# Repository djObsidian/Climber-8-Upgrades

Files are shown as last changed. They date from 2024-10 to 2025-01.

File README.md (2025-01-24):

# Climber-8-Upgrades
Some upgrades for the IDEX Climber-8A 3d printer. Includes improved printheads, direct drive extruder, print bed stabilization for high speed printing, configuration for Klipper with filament sensor support, fully functional COPY and MIRROR modes. 

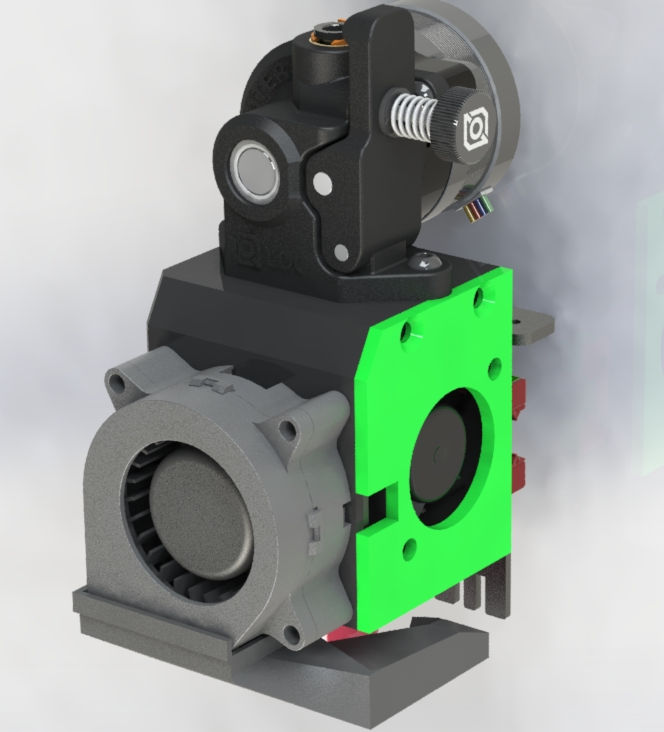
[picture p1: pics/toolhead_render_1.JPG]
Toolhead render


# Why?
Do you want to have two printers in one? Print with two completely different filaments? You don't like bedsilngers and prefer a faster and more compact printer? And not overpaying for a SnapMaker J1S or Ratrig V-Core? Then this upgrade kit is for you! Climber-8A is a very interesting 3D printer from aliexpress, the cheapest IDEX I could find that isn't a bedsilnger. Mechanically and electronically it is quite good, especially for its price, but has a number of flaws very undesirable in 2024, such as for example the bowden feed mechanism, low print speed, no input shaping and so on. This project is designed to fix them! 

# Printing 3d parts
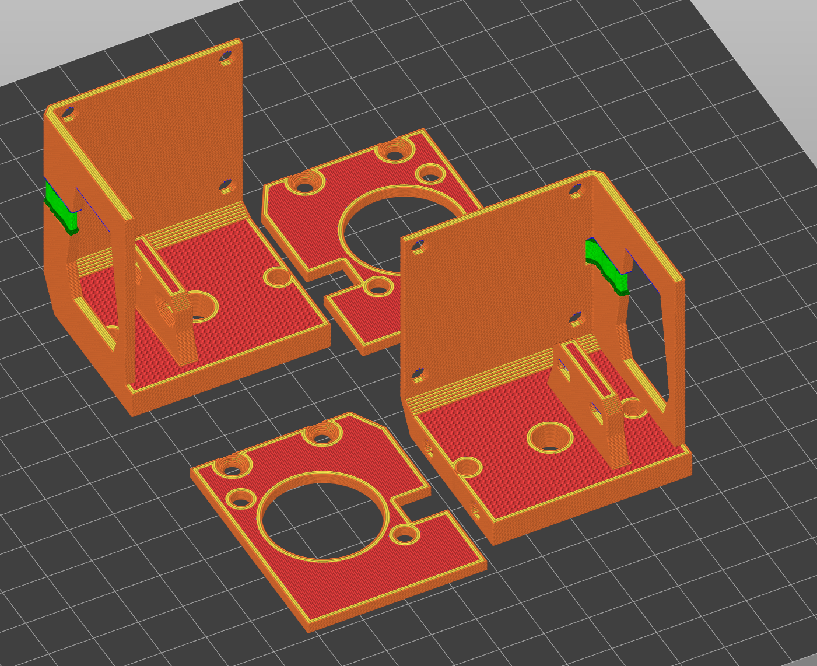
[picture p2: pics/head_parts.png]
Head parts

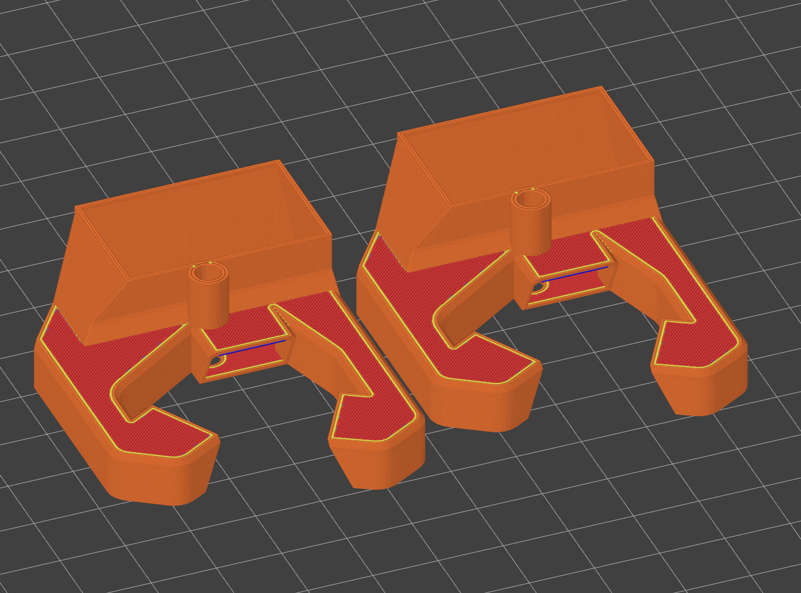
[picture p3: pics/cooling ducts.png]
Cooling ducts

You can find example print projects in *./toolhead* folder. They are configured for Creality K1. You may print everything as you want, but here're recommended settings:
| Parameter  | Value |
| --- | --- |
| Material  | ABS, ASA, PC, PA, or any other high temp non-flexible material  |
| Infill  | 80-100%  |
| Wall count | 3+ |
|Top/bottom layers| 3 for ducts, 4+ for toolhead|
| Layer height | <=0.12 for ducts, 0.2-0.28 for toolhead |
| Line width | 0.4-0.5 |
| Extra perimeters on overhangs | disabled for ducts |
| Thick bridges | enabled |

# Assembly instructions
[Illustrated step-by-step assembly instructions](assembly.md)

# Klipper config
Use following settings in order to compile MCU firmware. Flash as usual: rename file to firmware.bin, put it onto SD card, insert into 3d printer and boot. If you want to preserve original firmware, copy firmware.cur before flashing.
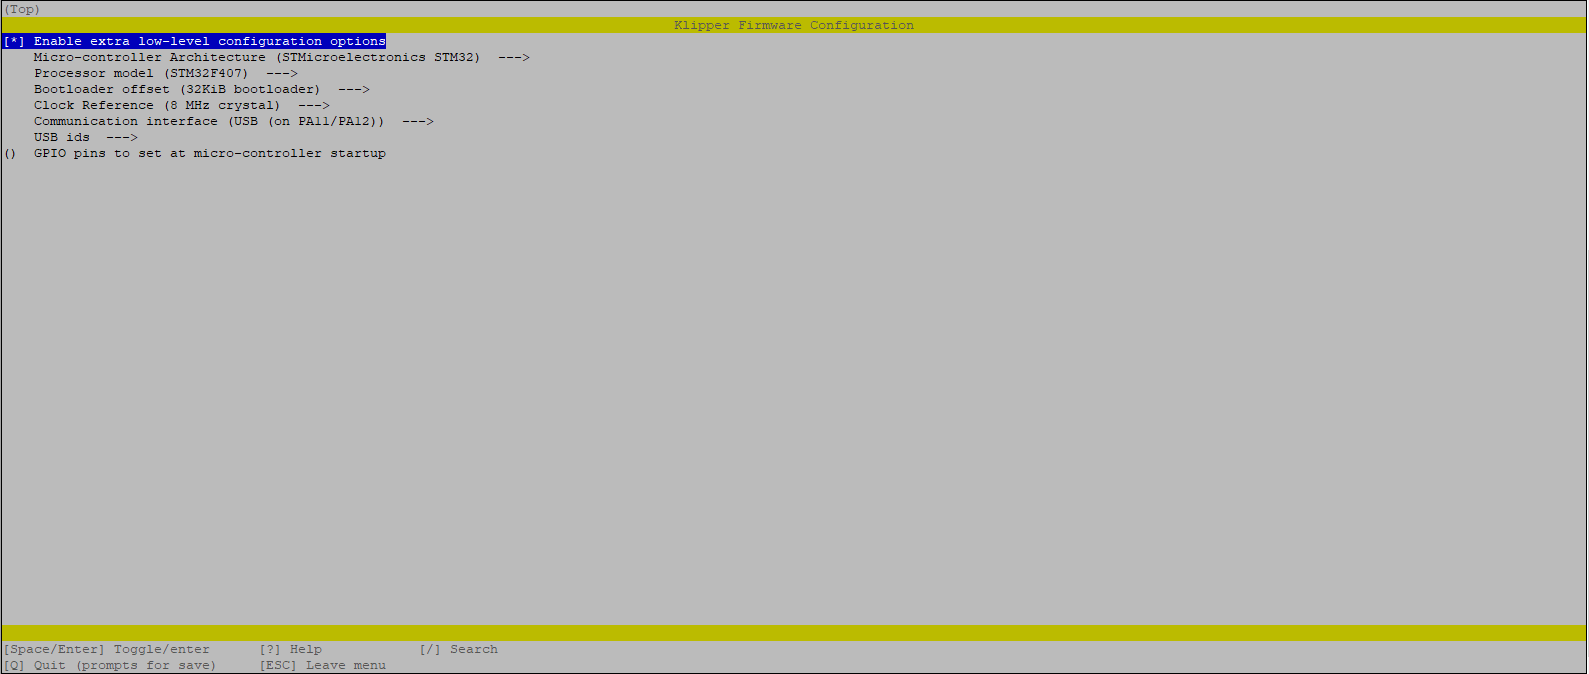
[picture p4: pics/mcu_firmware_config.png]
MCU config

Then simply import everything from klipper config folder. Change your [mcu] config accordingly. If you aren't using orbiter filament sensor, remove [include BOS.cfg] from printer.cfg. In this case you may want to write your own pause/resume macros. 

# Slicer config
Currentrly I support only prusaslicer. But porting to anything based on it shouldn't be too complicated.
Just import [normal mode](./prusaslicer%20config/config_normal_mode.ini) and [copy mode](./prusaslicer%20config/config_copy_mode.ini) into prusaslicer and set custom bed 3d model to [climber8 platform](./prusaslicer%20config/climber8_platform.STL).

# TODO Repo list
- [ ] Add BOM
- [X] Add assembly instructions
- [x] Add configuration instructions
- [x] Add parts printing instructions
- [x] Add slicer profiles
- [ ] Add board pinout and photos
- [ ] Add links to other people's used works

# TODO Project list
- [ ] Add spool holders and feed tubes
- [ ] Create better reinforcement for bed
- [ ] Reinforce the frame itself

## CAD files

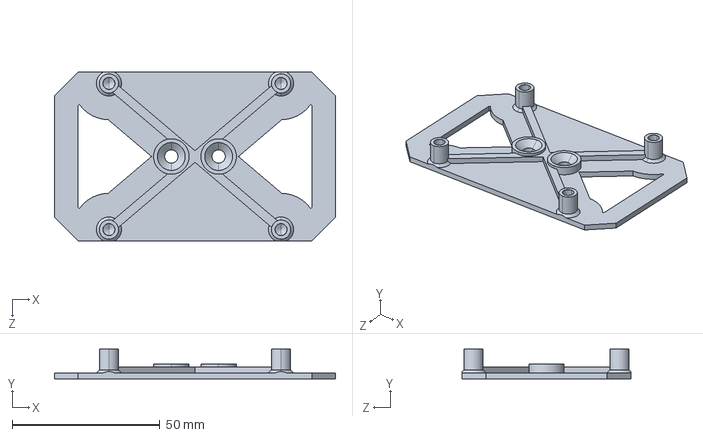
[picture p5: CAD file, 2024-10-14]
pi mount/pi_flat_mount.STEP
95.0 x 10.0 x 57.0 mm

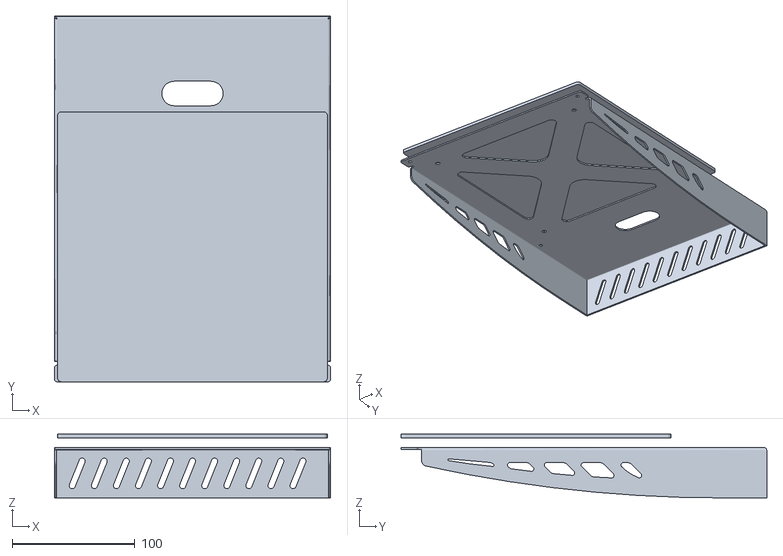
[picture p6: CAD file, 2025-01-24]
prusaslicer config/climber8_platform.STL
225.0 x 298.0 x 52.0

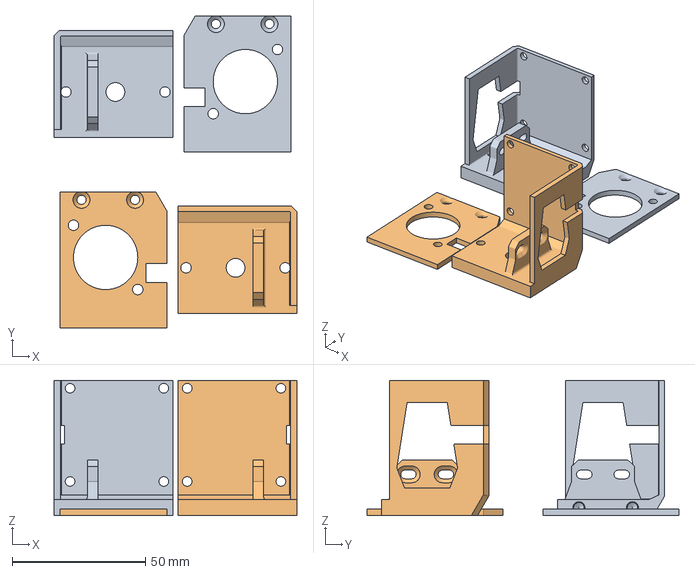
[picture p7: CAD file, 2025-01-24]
toolhead/Head v2.3mf
91.2 x 117.1 x 50.9 mm
Merged x 2

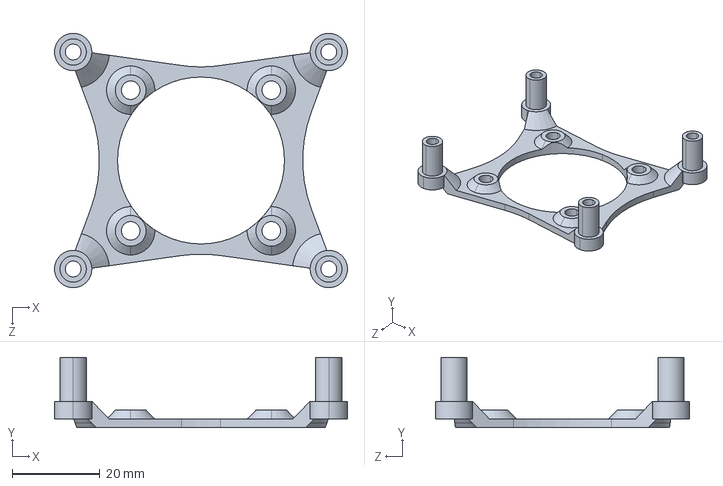
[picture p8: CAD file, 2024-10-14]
pi mount/pi fan.STEP
66.7 x 16.0 x 57.9 mm

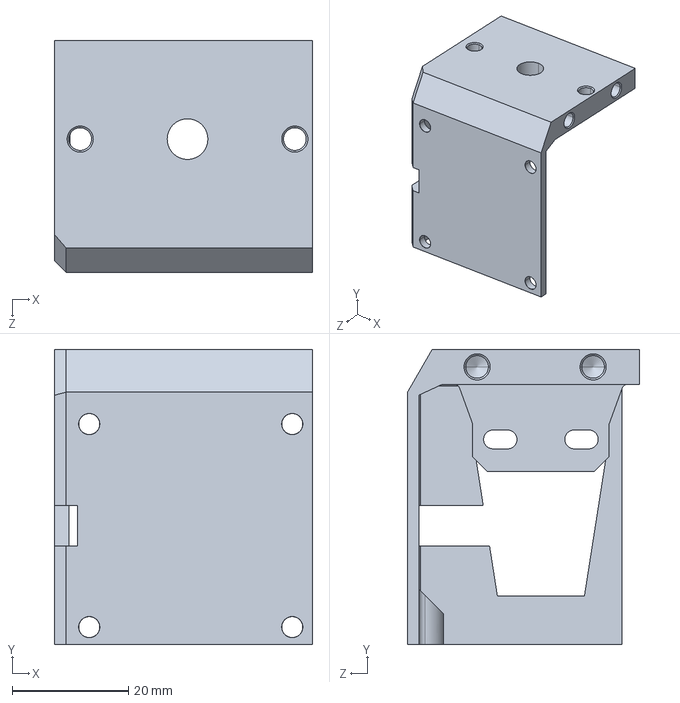
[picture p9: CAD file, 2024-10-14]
toolhead/ChasingV2.STEP
44.5 x 50.9 x 40.0 mm

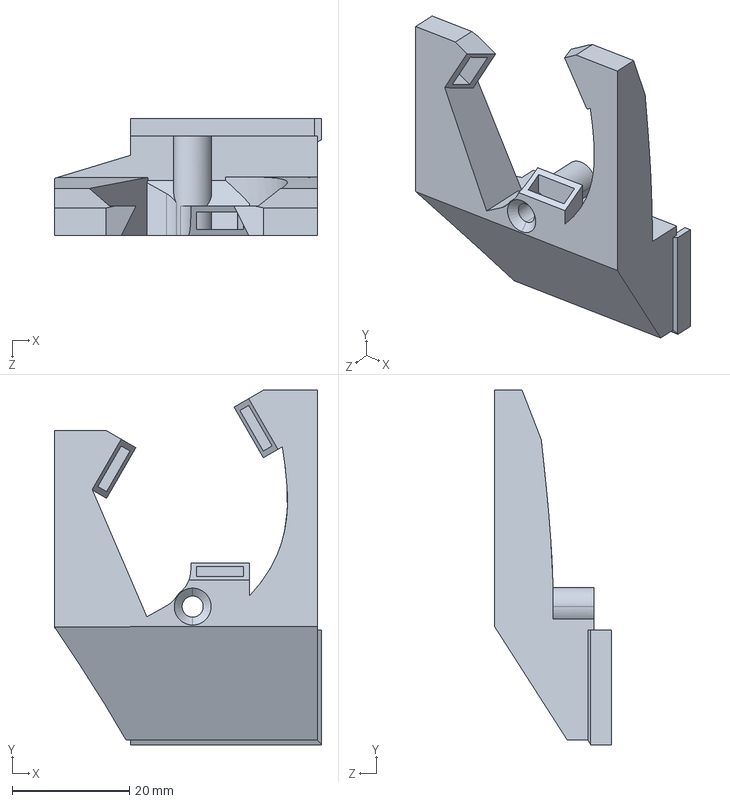
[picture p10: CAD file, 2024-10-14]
toolhead/Part Cooling.STEP
45.6 x 60.7 x 19.9 mm

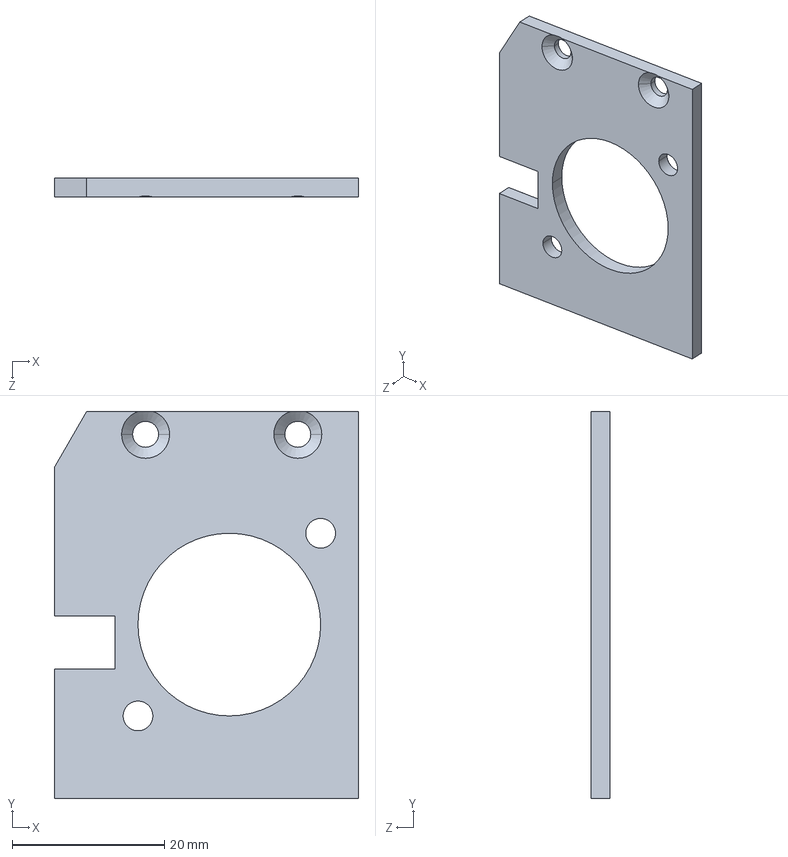
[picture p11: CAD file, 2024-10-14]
toolhead/FanSide.STEP
40.0 x 50.9 x 2.50 mm

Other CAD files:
toolhead/Part Cooling.3mf

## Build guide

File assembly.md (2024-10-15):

# Assembly instructions
## Wiring
The wiring is the weak part here and I don't provide instructions on it. Please figure it out yourself, there are not many wires in there
## Step 0
Disassemble existing toolheads. That should be easy, just unscrew and unplug everything. You don't need to disassemble heatsink of second toolhead, just unscrew it.
## Step 1
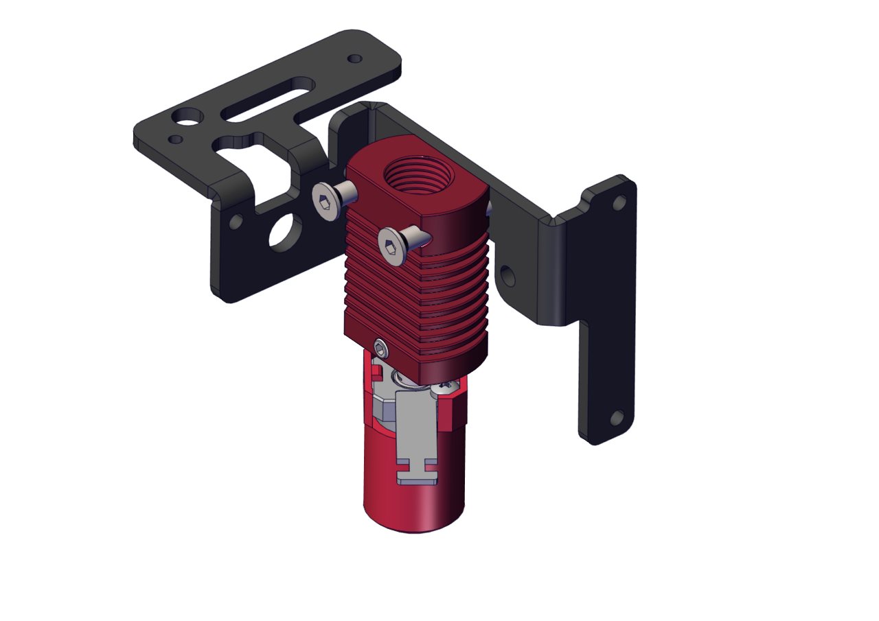
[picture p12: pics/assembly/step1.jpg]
Step 1

Assemble hotend. Temporarily secure it in place and do cable managment. For CHC you need to cut wires to length and crimp them with proper connectors. You also need to bend metal piece or unscrew it. Make sure wires fit inside chasing.

## Step 2
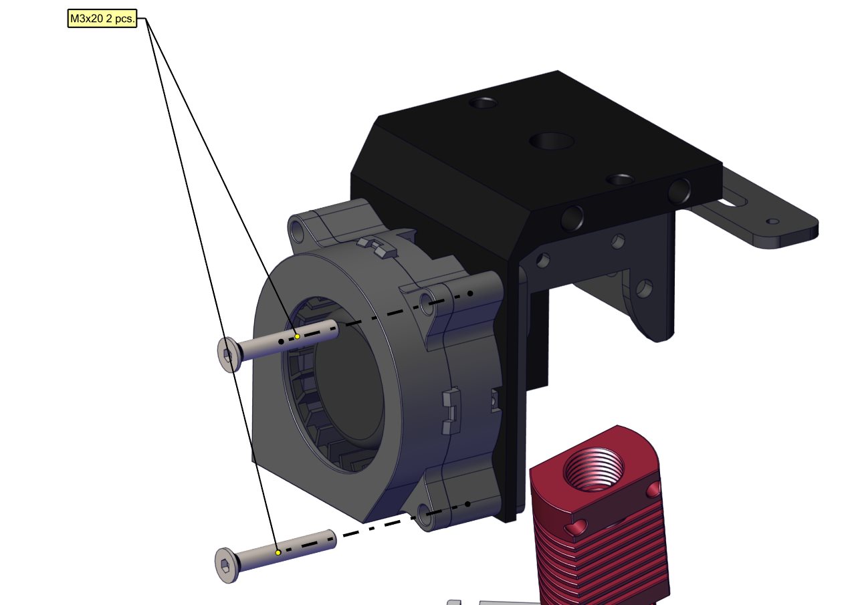
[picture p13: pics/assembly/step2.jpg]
Step 2

Remove hotend and secure blower fan and chasing to tool bracket. Using spacers is recommended

## Step 3
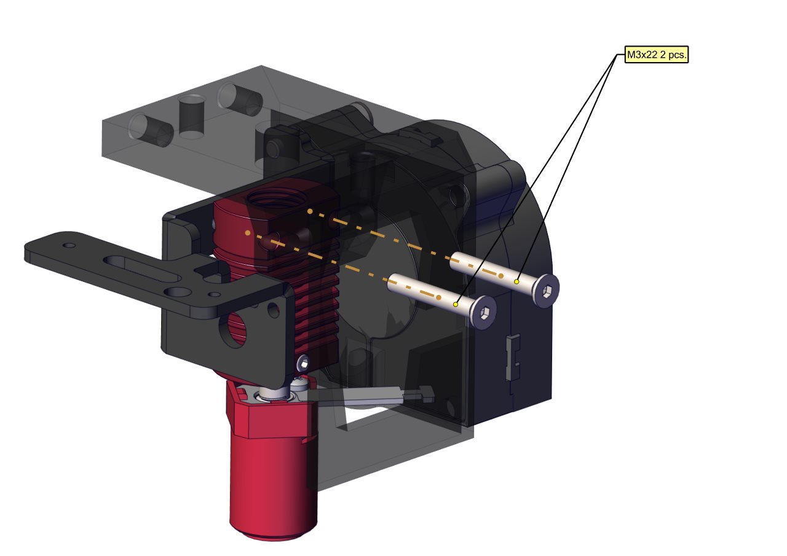
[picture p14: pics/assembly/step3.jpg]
Step 3

Move hotend to place and secure it with M3x22 screws. For right toolhead you may want to use M3x24 screw and nuts are nessecary sicne holes aren't threaded.

## Step 4
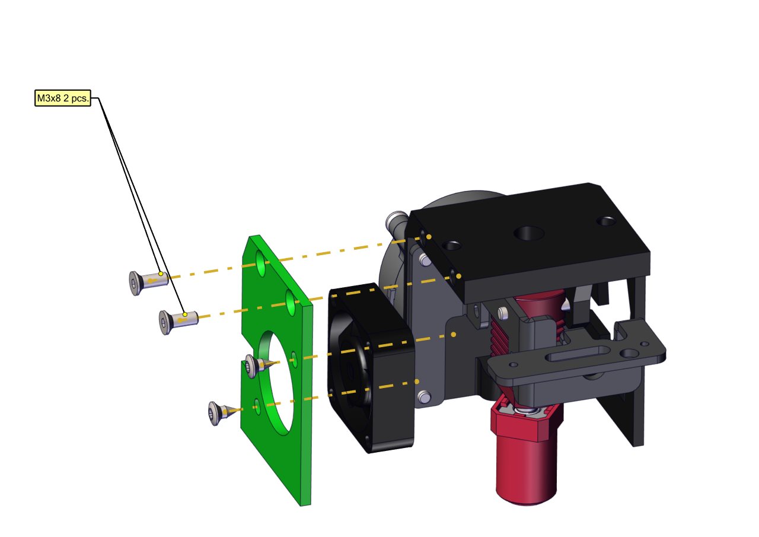
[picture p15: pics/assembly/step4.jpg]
Step 4

Assemble heatsink fan panel using same screws and secure it using two M3x8 screws. Side cut is for routing blower fan wires.

## Step 5
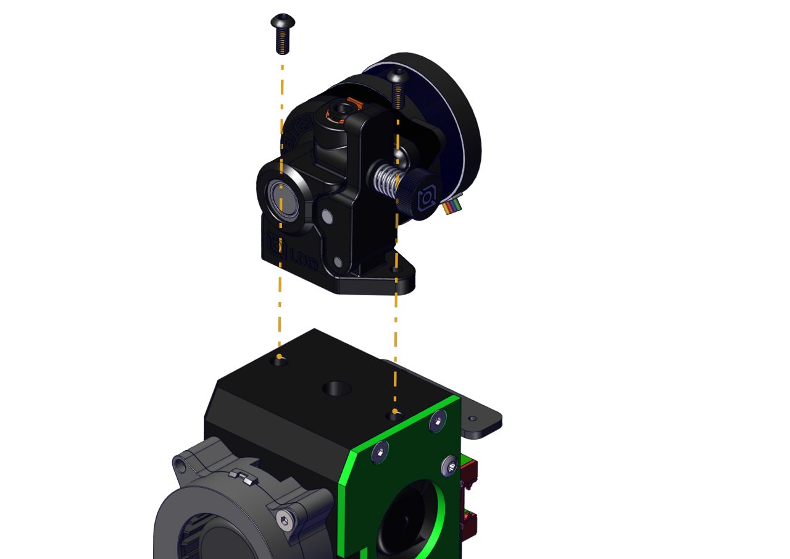
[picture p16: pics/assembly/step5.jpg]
Step 5

Cut PTFE tube and insert it in heatsink. You need a few mm to peek out to fit it in Orbiter.
Assemble Orbiter using appropriate manual and secure it using screws from it's kit.

## Step 6
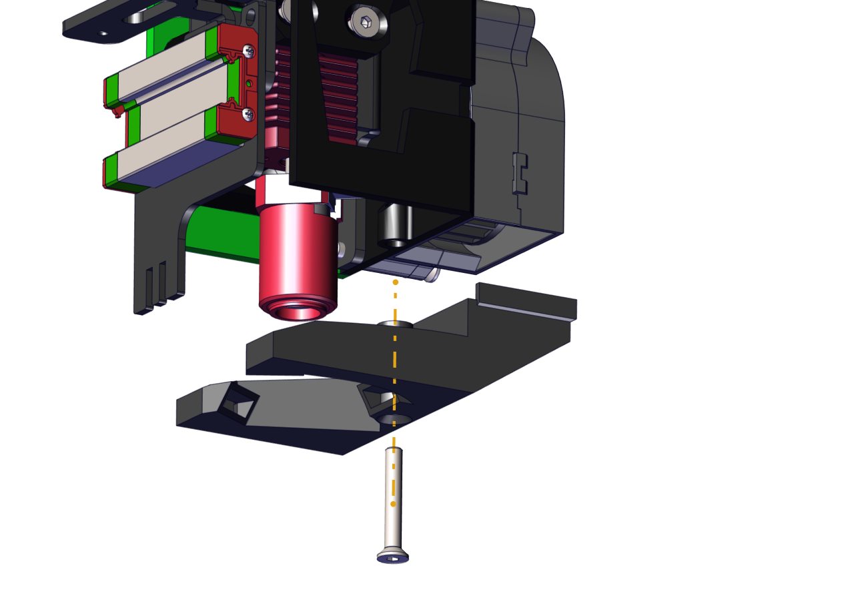
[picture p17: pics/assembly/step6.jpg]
Step 6

Secure fan ducts using M3x20 screw.

## Step 7
Now you can secure toolhead to printer following same steps as in printer's manual. You need to adjust bed endstop, unscrew it and cut plastic tube to length, so it stops at nozzle height or higher.

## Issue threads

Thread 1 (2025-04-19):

General questions/comments

kodonnell, 2025-04-19:
Very cool, good job = )

I got mine maybe 3-4 years ago, and set it up using klipper, and a 0.6mm nozzle and new cooling arrangement, plus a glass bed. But I was wanting to add direct drive to get some nicer prints (generally lots of stringing/blobs), and be able to handle TPU. And then I found you've done all the work already = )

Questions:

1. How long would it take you to make a BOM? I see that's on the TODO and I'm keen = ) Mostly which Orbiter version you used. Will the v2.5 work?
2. Did you do any of these? https://github.com/MrRandomStranger/XTLW-Climber-8/tree/main/Printer%20Fixes
3. The shaft for my Y-axis isn't concentric in the bearings. Do you have the same issue and did you fix that?
4. Generally: how have your prints improved after this mod? Have you tried ABS / TPU / (nylon?)?
5. Have you stuck with the hot-end? (Do you know any details for it if I want to get a replacement? E.g. is it just a standard one from another printer?)

Other ideas:

1. I always planned on making an enclosure, partly for rigidity, partly for a heated chamber and ventilation. Have you considered that? If I recall correctly, things weren't perfectly square when I set it up, so I was going to try to correct that with the frame.
2. I also just noticed that the build plate could be extended in the X direction to more like 300mm, which is reasonably significant vs the current 220. When I'm not wanting IDEX (i.e. most of the time) I was considering removing one extruders - and that'd allow me to use nearly all that 300mm. Have you looked into that? Just a new aluminium base plate (with mounting holes in the same location) and potentially a wider bed heater.

larsenv, 2025-04-19:
try getting a prusa

djObsidian, 2025-04-20:
Hi. I didn't think anyone would be interested in this project, I'll try to answer questions.
1. No idea honestly. You can figure out BOM mostly from assembly instructions. I used original orbiter v2
2. No, most of these problems are present in 8 and fixed in 8A version, which i have
3. Haven't looked into it, maybe, but I have no complaints about the quality of the prints
4. Very noticeable, but more because I didn't have the courage to tweak RepRap with bowden. I have more experience with klipper and direct type extruder. ABS was working fine before, it doesn't benefit from such changes, but TPU is a different story, this toolhead is able to print 65A TPU with no problems, at very low speed however.
5. It's all V6 type, so you wouldn't have any problems using heatblocks like V6, Volcano or something like that

I'm thinking of redesigning the print head, primarily to simplify nozzle replacement and z offset adjustment, possibly a bed level sensor
> build plate could be extended in the X direction to more like 300mm

It can't. It does look like there is space there, in fact given that there are two print heads, one just won't be able to use the whole bed, resting against the second one

kodonnell, 2025-04-21:
Thanks! Very useful.

I'll try get a list of updates from the manufacturer for the 8A vs 8.

> It can't. It does look like there is space there, in fact given that there are two print heads, one just won't be able to use the whole bed, resting against the second one

Yes, if you keep two print heads, each will only be able to use 260mm or so of the 300mm. But I don't understand why they're parked 45mm from the edge of the build plate ... couldn't all the 45mm be usable build plate?

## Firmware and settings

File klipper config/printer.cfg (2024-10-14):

### Climber 8A

[include OrbiterSensor.cfg]

[include idex.cfg]
[include fans.cfg]
[include display/*.cfg]
[include macros/*.cfg]


#[include OrbiterSensor_e1.cfg]

[save_variables]
filename: ~/printer_data/config/variables.cfg

[mcu]
serial: /dev/serial/by-id/usb-Klipper_stm32f407xx_2D002B001651333131383237-if00
#serial: /dev/serial/by-id/usb-Silicon_Labs_CP2104_USB_to_UART_Bridge_Controller_02L2SVPM-if00-port0
restart_method: command
#baud: 750000

[virtual_sdcard]
path: /home/biqu/printer_data/gcodes
on_error_gcode: CANCEL_PRINT

[printer]
kinematics: cartesian
max_velocity: 500
max_accel: 10000
max_z_velocity: 25
max_z_accel: 30

#######################################################################################################################
# Definition for z. FYI Z_CS_PIN = PD5
#######################################################################################################################

[stepper_z]
step_pin: PD6
dir_pin: !PD7
enable_pin: !PB6
endstop_pin: !PB11
microsteps: 16
rotation_distance: 8
#position_endstop: -5
position_min: -8 # When we set global and extruder1 offset a little negative ...
position_max: 240
homing_speed: 20

[tmc2208 stepper_z]
uart_pin: PD5
run_current: 0.6
stealthchop_threshold: 999999

[stepper_y]
step_pin: PB8
dir_pin: PB9
enable_pin: !PE0
endstop_pin: !PB10
microsteps: 16
rotation_distance: 40
position_endstop: 205
position_max: 205
position_min:-15
homing_speed: 50

[tmc2208 stepper_y]
uart_pin: PB7
run_current: 1.2
stealthchop_threshold: 999999

[stepper_x]
step_pin: PC13
dir_pin: !PC14
enable_pin: !PC15
microsteps: 16
rotation_distance: 40
endstop_pin: !PC2
position_endstop: -48
position_min:-48
position_max: 200
homing_speed: 50

[tmc2208 stepper_x]
uart_pin: PE5
run_current: 0.8
stealthchop_threshold: 999999


[dual_carriage]
axis: x
step_pin: PE2
dir_pin: !PE3
enable_pin: !PE4
endstop_pin: !PC0
microsteps: 16
rotation_distance: 40
position_min: 0
position_endstop: 262
position_max: 262
homing_speed: 50

[tmc2208 dual_carriage]
uart_pin: PE1
run_current: 0.8
stealthchop_threshold: 999999

# Extruder config

[extruder]
step_pin: PD1
dir_pin: PD3
enable_pin: !PD4
microsteps: 16
full_steps_per_rotation: 200
rotation_distance: 4.637
nozzle_diameter: 0.400                             #define nozzle diameter
filament_diameter: 1.750
max_extrude_only_distance: 500
max_extrude_only_velocity: 120
pressure_advance: 0.025                         #to be calibrated
pressure_advance_smooth_time: 0.03     #to be calibrated
heater_pin: PA1
sensor_type: ATC Semitec 104NT-4-R025H42G
sensor_pin: PC3
#control: pid
#pid_kp: 19.843
#pid_ki: 0.973
#pid_kd: 101.201
min_temp: 0
max_temp: 300
min_extrude_temp: 180
max_extrude_only_distance: 100

[tmc2208 extruder]
uart_pin: PD0
interpolate: true
run_current: 0.75 #**
sense_resistor: 0.11 #**
stealthchop_threshold: 0
driver_TBL: 0
driver_HEND: 6
driver_HSTRT: 7
driver_TOFF: 4

[verify_heater extruder]
check_gain_time: 60


# Extruder1 config

[extruder1]
step_pin: PC6
dir_pin: PA8
enable_pin: !PA15
microsteps: 16
full_steps_per_rotation: 200
rotation_distance: 4.637
nozzle_diameter: 0.400                             #define nozzle diameter
filament_diameter: 1.750
max_extrude_only_distance: 500
max_extrude_only_velocity: 120
pressure_advance: 0.025                         #to be calibrated
pressure_advance_smooth_time: 0.03     #to be calibrated
heater_pin: PC7
sensor_type: ATC Semitec 104NT-4-R025H42G
sensor_pin: PC1
control = pid
pid_kp = 20.753
pid_ki = 1.456
pid_kd = 73.932
min_temp: 0
max_temp: 300
min_extrude_temp: 180
max_extrude_only_distance: 100

[tmc2208 extruder1]
uart_pin: PD15
interpolate: true
run_current: 0.75 #**
sense_resistor: 0.11 #**
stealthchop_threshold: 0
driver_TBL: 0
driver_HEND: 6
driver_HSTRT: 7
driver_TOFF: 4

[verify_heater extruder1]
check_gain_time: 60

[heater_bed]
heater_pin: PB0
sensor_type: Generic 3950
sensor_pin: PC5
#control: pid
#pid_Kp: 54.027
#pid_Ki: 0.770
#pid_Kd: 948.182
min_temp: 0
max_temp: 110 # should be 120 according to specs, but let's be safe as we're only doing PLA.

# Other
[pause_resume]


#######################################################################################################################
# Display: BTT Mini 12864 Panel v1.0. In Marlin set as Fystec Mini 12864 v2.1 ...
#######################################################################################################################

[display]
lcd_type: uc1701
cs_pin: PB2
a0_pin: PE12
rst_pin: PE13
contrast: 63
encoder_pins: ^PD13, ^PD12
click_pin: ^!PE11
spi_software_miso_pin: PA6
spi_software_mosi_pin: PA7
spi_software_sclk_pin: PA5
display_group: _homescreen



[output_pin beeper]
pin: PE10

[neopixel btt_mini12864]
pin: PE14
chain_count: 3
color_order: RGB
initial_RED: 0.5
initial_GREEN: 0.5
initial_BLUE: 0


[gcode_macro CANCEL_PRINT]
rename_existing: BASE_CANCEL_PRINT
gcode:
    TURN_OFF_HEATERS
    CLEAR_PAUSE
    SDCARD_RESET_FILE
    SET_SKEW CLEAR=1
    M106 S0
    BASE_CANCEL_PRINT

[bed_screws]
screw1: 5, 0
screw2: 5, 190
screw3: 200, 190
screw4: 200, 0

[input_shaper]

[exclude_object]

# [mcu blackipll]
# serial: /dev/serial/by-id/usb-Klipper_stm32f401xc_320062001051353331363933-if00

# [adxl345]
# cs_pin: blackipll:PA4
# spi_software_sclk_pin: blackipll: PA5
# spi_software_mosi_pin: blackipll: PA7
# spi_software_miso_pin: blackipll: PA6
# axes_map: y, -x, z

# [resonance_tester]
# accel_chip: adxl345
# probe_points:
#     115, 115, 50  # an example

#*# <---------------------- SAVE_CONFIG ---------------------->
#*# DO NOT EDIT THIS BLOCK OR BELOW. The contents are auto-generated.
#*#
#*# [extruder]
#*# control = pid
#*# pid_kp = 20.753
#*# pid_ki = 1.456
#*# pid_kd = 73.932
#*#
#*# [heater_bed]
#*# control = pid
#*# pid_kp = 75.270
#*# pid_ki = 1.713
#*# pid_kd = 827.025
#*#
#*# [stepper_z]
#*# position_endstop = -4.215
#*#
#*# [input_shaper]
#*# shaper_type_x = mzv
#*# shaper_freq_x = 86.4
#*# shaper_type_y = mzv
#*# shaper_freq_y = 66.4

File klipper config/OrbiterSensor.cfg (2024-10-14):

#################################################################################################################
################################# Orbiter Sensor CONFIGURATION ##################################################
#################################################################################################################

#config file version v2.2.04
#release date: 23.09.2023

# PAUSE and RESUME macros are defined at the end of this config file.
# If you prefer using your own p[lease delete them, otherwise define parking position below.

#################################################################################################################
################################# CHANGE HERE MACRO CONFIGURABLES################################################
#################################################################################################################

[gcode_macro _SENSOR_VARIABLES]         # change here macro configurables, enable disable functions!*************************
variable_filament_load_temp     :235    # temperature to heat up hotend for filament loading, default is 235
variable_filament_unload_temp   :220    # temperature to heat up hotend for filament un-loading, default is 185
variable_filament_load_min_temp :200    # minimum hotend set temperature allowed in filament load macro, default is 190
variable_nozzle_purge_length    :100    # filament extrude amount during load sequenc, hotend purge from old filament, default is 200
variable_nozzle_purge_speed     :450    # filament extrude speed in mm/min adjust this value lower if flow is too high and extruder skips during loading, default is 300
variable_unload_distance        :65     # filament retract distance for unload procedure. this length shall be long enough to extract the filament above the drive gears
variable_disable_autoload       :False  # disable filament autoload feature by setting this variable True
variable_disable_runnout        :False  # disable runnout by setting this variable True
variable_disable_autounload     :False  # disable auto unload filament by setting this variable to True
variable_enable_beep            :True   # uses M300 sound feature, set it True to enable
variable_park_position_x        :0    # edit your X parking position here for pause macro trigerred by runnout
variable_park_position_u        :260    # edit your U parking position here for pause macro trigerred by runnout
variable_park_position_y        :30     # edit your Y parking position here for pause macro trigerred by runnout
variable_park_lift_z            :10     # edit your Z lift amount for parking position here, default is 10
Variable_park_retraction        :1      # edit your retraction amount for parking, default is 1
gcode:

#///////////////////////////filament sensor button macros/////////////////////////////////////////////////
[gcode_button filament_sense]
pin: !PC4 # remove the negation "!" for sensor v1 - use just PA9 as example
press_gcode: # sensor released  -runnout detected!
  runnout_init
release_gcode: #gcode macro for filament auto-load, sensor pressed
  ACTIVATE_EXTRUDER EXTRUDER=extruder
  filament_load_init
#********************************************************************************************************

#////////////////////////////////////////Filament Unload macros/////////////////////////////////////////////////
[gcode_button filament_unload]
pin: !PB15 # remove the negation "!" for sensor v1 - use just PA9 as example
release_gcode:  # filament unload procedure   
  M118 Unload call extruder 0
  T0
  filament_unload_init
press_gcode: # do not add any macro call here

#################################################################################################################################
####################################### DO NOT CHANGE ANYTHING BELOW THIS LINE!!! ###############################################
#################################################################################################################################
####################################### UNLESS YOU KNOW WHAT YOU ARE DOING OR YOU ARE BORED AND NEED TO DO SOMETHING OR YOU ARE ALONE AND NEED SOMETHING TO MESS UP YOUR LIFE OR YOU CAN DO IT BETTER THAN ME OR YOU ARE A REAL SMARTASS OR JUST BECAUSE YOU CAN OR YOU RUN OUT OF BEAR OR HAS NOTHING BETTER TO DO OR ANY UNREASONABLE REASON
#################################################################################################################################

[respond]
default_type: echo

[force_move]
enable_force_move: True

[gcode_macro runnout_init]
gcode:
  {% set sensor = printer['gcode_macro _SENSOR_VARIABLES'] %}  
  {% if (printer.print_stats.state == "printing") %}      
    {% if(sensor.disable_runnout|lower == 'false') %}
      filament_change_state1
    {% else %}
    M118 Filament runnout is disabled in the sensor config file!   
    {% endif %}     
  {% endif %} 
  UPDATE_DELAYED_GCODE ID=clear_loadbusy DURATION=2
  UPDATE_DELAYED_GCODE ID=clear_unloadbusy DURATION=2    
  SET_GCODE_VARIABLE MACRO=filament_unload VARIABLE=filamentpresent VALUE=0

[gcode_macro filament_change_state1]
variable_changebusy: 0
variable_temp_target: 0
gcode:
  {% set sensor = printer['gcode_macro _SENSOR_VARIABLES'] %}  
  {% if changebusy == 0 %}
    PAUSE # call printer pause macro      
    SET_GCODE_VARIABLE MACRO=filament_change_state1 VARIABLE=changebusy VALUE=1       
    M118 Filament runnout!       
    filament_change_state2     # comment this line if you do not want to automatically unload filament in case there is a runnout detected.
  {% else %}
  {% endif %}

[gcode_macro filament_change_state2]
gcode:
  {% set sensor = printer['gcode_macro _SENSOR_VARIABLES'] %}  
  SET_GCODE_VARIABLE MACRO=filament_load VARIABLE=loadbusy VALUE=1      
  {% if (sensor.enable_beep|lower == 'true') %} 
    M300 # beep sound
  {% endif %}
  M118 Unloading filament...   
  M83
  G92 E0   
  # {% if printer[printer.toolhead.extruder].temperature < 185 %} # hardcoded threshold
  {% if (printer.extruder.can_extrude|lower != 'true')%} # checing for minimum extrusion temperature
        # check if temperature is over the minimum extrusion temp. min_extrude_temp must be defined in the extruder config (to about 185)
      M118 Hotend heating!        
      SET_HEATER_TEMPERATURE HEATER=extruder TARGET={sensor.filament_unload_temp} # restore user temp if it was set before loading
      TEMPERATURE_WAIT SENSOR=extruder MINIMUM={sensor.filament_unload_temp} #wait for reaching filament unload temp
      {% endif %}     
  {% if(printer.extruder.target == 0) %} # checing for set temperature if is zero than set to 200 / hotend hot but cooling due to set target temp 0
      SET_HEATER_TEMPERATURE HEATER=extruder TARGET={sensor.filament_unload_temp} # restore user temp if it was set before loading
      TEMPERATURE_WAIT SENSOR=extruder MINIMUM={sensor.filament_unload_temp} #wait for reaching filament unload temp
  {% endif %} 
  G0 E-5 F3600 	#extract filament to cold end
  G4 P2000 # wait for two seconds
  G0 E5 F3600 # push the filament back 
  G0 E-5 F3600 	#extract filament to cold end
  G0 E-{sensor.unload_distance} F300	# continue extraction slow allow filament to be cooled enough before reaches the gears  
  M400   
  M118 Load new filament! Wait until is loaded, then resume printing.  
  SET_HEATER_TEMPERATURE HEATER=extruder TARGET=0 # swicth off heater
  UPDATE_DELAYED_GCODE ID=clear_loadbusy DURATION=2.5 # timing must be set to clear delay plus 0.5s. is due to wait to remove filament before starting load even in case there is a blob at the tip of the extracted filament which woudl trigger the sensor twice

#############################################END filament auto load macro section END***********************************************************

[gcode_macro filament_load_init]
gcode:
  {% set sensor = printer['gcode_macro _SENSOR_VARIABLES'] %}
  {% if (printer.print_stats.state != "printing") %}
    {% if(sensor.disable_autoload|lower == 'false') %}
      filament_load
    {% else %}
    M118 Filament auto-load is disabled in the sensor config file!   
    {% endif %} 
  {% else %}    
    M118 Printing! Can't load filament right now!    
  {% endif %} 
  SET_GCODE_VARIABLE MACRO=filament_unload VARIABLE=filamentpresent VALUE=1
  UPDATE_DELAYED_GCODE ID=clear_changebusy DURATION=2
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

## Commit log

2024-10-14 Added head files and config
    [ChasingV2.STEP, FanSide.STEP, OrbiterSensor.cfg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]
2024-10-15 Assembly instructions
2024-10-15 Update README.md
    Illustrated step-by-step assembly instructions
2025-01-24 Printing instructions, slicer configs and klipper config
    [Head v2.3mf, Part Cooling.3mf, climber8_platform.STL]
